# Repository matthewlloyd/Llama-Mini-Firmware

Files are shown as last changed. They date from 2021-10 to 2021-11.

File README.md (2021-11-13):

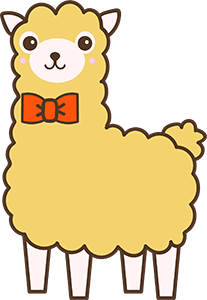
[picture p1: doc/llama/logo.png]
Llama Mini
# 

# Llama Mini

[]()

### Unofficial Firmware for the Prusa Mini and Mini+

One of Prusa's llamas escaped from HQ (:llama::running_man:) and decided to make his
own version of the firmware for the Prusa Mini. He's added quite
a few goodies:

* **Hotend fan speed**: Adds a menu option to unlock the hotend fan speed
  and increase it from the Prusa Firmware's default 38% to anywhere from 50-100%.
* **Skew compensation**: Turns on skew compensation in Marlin and allows it
  to be configured directly through the Settings menu or with `M852`.
* **OctoPrint screen**: Adds support for `M73` (print progress) and `M117`
  (LCD messages).
* **Sound**: Adds support for `M300` (play a sound).
* **PID tuning**: Automatically writes PID settings to EEPROM after `M303 U1` (autotune),
  `M301` (set hotend PID), and `M304` (set bed PID).
* **Max Temps**: Raises the maximum bed temperature from 100C to 110C
  and nozzle temperature from 290C to 300C (use with caution!).

All settings are automatically saved to EEPROM and loaded on boot.

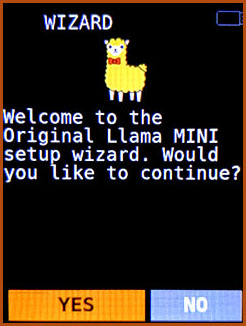
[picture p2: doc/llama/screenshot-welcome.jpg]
Welcome

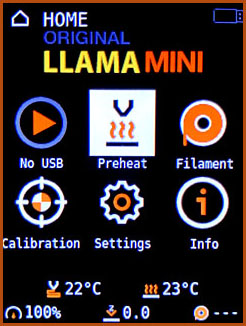
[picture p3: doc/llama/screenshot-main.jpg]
Main

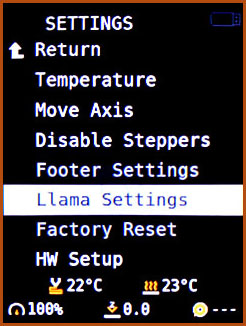
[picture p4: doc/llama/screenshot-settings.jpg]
Settings

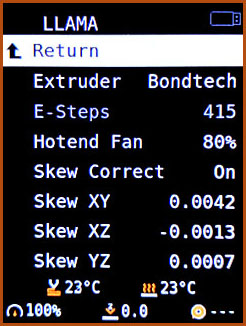
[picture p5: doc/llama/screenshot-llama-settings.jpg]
Llama Settings

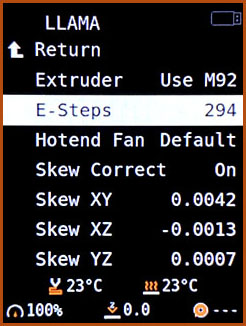
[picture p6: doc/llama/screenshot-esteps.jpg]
E-Steps

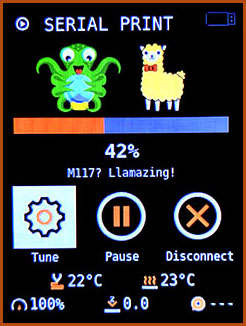
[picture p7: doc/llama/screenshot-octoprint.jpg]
Octoprint


#### Feed the Llama

This plugin is developed in my spare time. If you like it, please
consider supporting further development and updates by making a donation.



---

## Installing Livestock

### Jailbreak your Mini

You will need to cut out Prusa's appendix to install custom firmware.
Follow the instructions [here](https://help.prusa3d.com/en/article/flashing-custom-firmware-mini_14/).
This is irreversible and voids the warranty, although in the US
you are protected by the [Magnuson-Moss Warranty Act](https://www.ftc.gov/news-events/press-releases/2018/04/ftc-staff-warns-companies-it-illegal-condition-warranty-coverage).

Of course you could always buy a second Buddy board and let your Llama
run wild on that instead.

Alternatively, if you are good at very fine pitch soldering, you could
lift the BOOT0 pin off the board entirely and make your own jumpers
to connect it directly to 3.3V or GND as you need (the appendix merely
[shorts BOOT0 directly to GND](https://hackaday.com/2019/12/16/prusa-dares-you-to-break-their-latest-printer/)).

Once you have done that, you can live and let live-stock.

### Flash Llama

Whenever you install new firmware, it's good practice to make a note of your
settings first, particularly your Live Z Offset and your skew coefficients
if you already have Llama installed.

Download the latest release [here](https://github.com/matthewlloyd/Llama-Mini-Firmware/releases).
Copy the `.bbf` file to the root of your USB flash drive.
Follow the instructions [here](https://help.prusa3d.com/en/guide/how-to-update-firmware-mini-mini_128421/)
to install the firmware. The bootloader will warn you the signature is
incorrect - select "Ignore".

### First Run

If you lose your Prusa EEPROM settings during the upgrade process,
when you first run the firmware, Prusa will send you to the initial
calibration wizard. This can be a problem if you need to set custom e-steps
before printing anything. Just skip the initial setup wizard,
use the Llama Settings menu to configure your e-steps, and
then rerun the setup wizard manually.

### Livestock to Stock

Download Prusa's stock firmware [here](https://www.prusa3d.com/drivers/).
The bootloader might not let you downgrade the firmware unless you
explicitly give permission. Go to the Settings menu, scroll down to "FW Upgrade",
and change the option to "On Restart Older" (this option is only available
in Llama firmware).

To reflash the board in DFU mode, [see below](#flashing-in-dfu-mode).

---

## Configuration

To configure Llama settings, open the Settings menu and select "Llama Settings".
Llogical!

### Configuring E-steps

New in v1.0.7: This can now be done using Prusa's own "Experimental Settings" menu,
which is shown by default as a menu item next to "Llama Settings" in this firmware.

#### For Llama versions v1.0.6 and below

Select "Extruder" and click to select one of:

- **Prusa**. Stock e-steps for the stock extruder.
- **Bondtech**. Preset e-steps for the [Bondtech extruder upgrade](https://www.bondtech.se/product/prusa-mini/).
  This option assumes you have reversed the motor wiring as per Bondtech's instructions -
  if you haven't, you can reverse the extruder motor direction using the "Reverse E" option.
- **Custom**. The e-steps can be configured using the jog wheel, or by
  sending the `M92 E<steps>` command.

Whether you use a preset, or set custom e-steps via the jog wheel
or `M92`, your settings will automatically be saved to EEPROM.
You do not need to use `M500`.

### Configuring Hotend Fan Speed

The Prusa firmware limits the hotend fan speed to 38% because a happy user is a user with
an underperforming but quiet machine. The fan is capable of running at much
higher RPMs. There are a few reasons you might want to do this:

- Reduce heat creep.
- Print higher temperature filaments.
- Change the fan to one which requires full voltage, e.g. a Noctua.

This menu option allows you to set the hotend fan speed anywhere from 50% to 100%,
in 10% steps. The setting is automatically saved to EEPROM and restored on boot.

### Configuring Skew Compensation

The Prusa Mini+ is inherently prone to skew, by virtue of its cantilever
design. It is normal to see skew on all three axes. This affects the precision
of any parts you print.

Prusa disabled skew compensation in Marlin, because a happy user is a user
with an imprecise but easy to use machine. Lluckily our Llama has reenabled it.
All three skew compensation coefficients are available for use - I for XY, J for XZ,
and K for YZ.

Note it is always preferable to remove as much skew as possible through physical
adjustments before using firmware skew compensation. For excellent
instructions, read [this post on Prusa's forum](https://forum.prusaprinters.org/forum/hardware-firmware-and-software-help/oh-no-were-skewed-prusa-mini-edition/).

See [the section below](#calibrating-skew) for a guide on how to measure skew
and compute the coefficients. You can use the jog wheel to set
the coefficients in this menu, or use `M852`. Either way, the settings
will automatically be saved to EEPROM - you do not need to use `M500`.
Be sure to set `Skew Correct` to `On` for the settings to be used.

Be careful with large skew correction factors - it is possible to go past
the min or max travel on the X and Y axes while printing or even during
mesh bed leveling. A skew factor of e.g. 0.01 equates to
`0.01 * 180mm = 1.8mm` of movement at the far end of the bed,
so your usable print area will be reduced accordingly.

### Configuring PID Parameters

The stock firmware allows you to run an `M303` PID autotune, but the new
settings are lost on reset. In Llama, PID settings are *automatically* written
to EEPROM after any command that updates Marlin's PID values, which could be
an `M301` (set hotend PID), `M304` (set bed PID), or an `M303 U1` (autotune and
use the PID result). These values will then be restored on reset, too. You do not
need to use `M500`.

If you need to restore the default PID values, they can be reset by running
the following commands:

* Hotend: `M301 P7.00 I0.50 D45.00`
* Bed: `M304 P120.00 I1.50 D600.0`

Note that if you run `M303` (autotune) without the `U1` parameter, Marlin
will just print out the suggested PID values without changing the settings,
and they won't get written to EEPROM.

---

### Print Progress

Note that to take advantage of Llama's `M73` support with [OctoPrint](https://octoprint.org),
you will need to install one or more plugins. I recommend these three:

- [Print Time Genius](https://plugins.octoprint.org/plugins/PrintTimeGenius/),
  an excellent plugin to compute accurate progress estimates. It doesn't send
  `M73` or `M117` on its own, so you will need the next two plugins too.
- [DisplayLayerProgress](https://github.com/OllisGit/OctoPrint-DisplayLayerProgress).
  Turn on the "Printer Display" option and customize to your preference.
  This will send `M117`. I like to set the message to `[printtime_left] L=[current_layer]/[total_layers]`
  and the update interval to 10 seconds.
- [M73 Progress](https://plugins.octoprint.org/plugins/m73progress/).
  Be sure to enable the "Use time estimate" option.

It may also be possible to arrange for your slicer to insert these commands,
but the result will not be as accurate.

---

## Calibrating Skew

Measuring skew on all three axes at once can be done by simply printing
[this compact calibration tower](doc/llama/skew.stl):

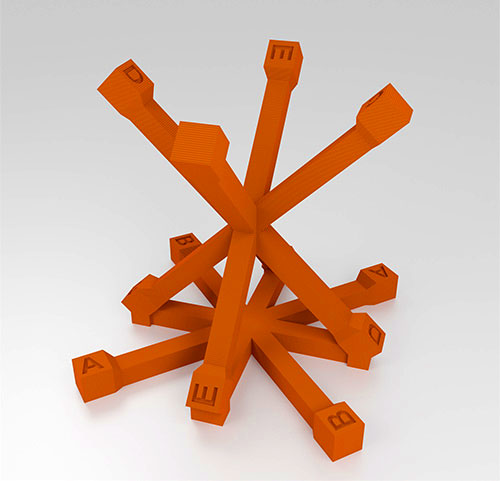
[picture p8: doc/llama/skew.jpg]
Skew Tower


Turn off skew correction before you print. Use a normal layer height
(0.15mm) and no supports. Do not rotate the model in your slicer -
it must be printed in the same orientation as supplied in the STL.

Then, make a copy of [this spreadsheet](https://bit.ly/2SJ1hAU).
Use [calipers](https://amzn.to/3vVRgOl) to measure the six diagonals,
conveniently labeled A to F, and type the measurements
into the spreadsheet. It will calculate your three skew correction factors.
You can either input them using the Llama menu and jogwheel as described above,
or send them directly to the printer using the supplied `M852` command.

If you want to check your calibration is accurate,
print the same tower with skew correction enabled. The diagonals should
then all have the same length (within measurement error of course).

---

### Flashing in DFU Mode

If the bootloader refuses to accept firmware from a USB flash drive,
it's possible to flash the board directly in DFU mode.

Compile the firmware and build a DFU file:

```
$ python3 utils/build.py --generate-dfu --bootloader yes
```

If you built it from another machine, copy it to your Pi:

```
$ scp build/mini_release_boot/firmware.dfu <user>@<pi-host>:~/
```

Put your Buddy board in DFU mode by placing a jumper across the relevant pins
and resetting. If you have a 3-pin header next to the appendix (older versions
of the board), put the jumper between BOOT0 and 3.3V. If you have a 2-pin header,
just add a jumper.

Then flash from your Pi:

```
$ lsusb
Bus 001 Device 010: ID 0483:df11 STMicroelectronics STM Device in DFU Mode
$ sudo apt install dfu-util
$ dfu-util -a 0 -D firmware.dfu
```

Don't forget to remove the jumper before resetting.

---

*Copyright (C) 2021 Matthew Lloyd*

## Original Prusa Mini Firmware README
<details>
<summary>Click to expand!</summary>

# Buddy

Build Status (https://holly.prusa3d.com/job/Prusa-Firmware-Buddy/job/Multibranch/job/master/)

This repository includes source code and firmware releases for the Original Prusa 3D printers based on the 32-bit ARM microcontrollers.

The currently supported model is:
- Original Prusa MINI

## Getting Started

### Requirements

- Python 3.6 or newer
- python3-pip

### Cloning this repository

Run `git clone https://github.com/prusa3d/Prusa-Firmware-Buddy.git`.

### Building (on all platforms, without an IDE)

Run `python utils/build.py`. The binaries are then going to be stored under `./build/products`.

- Without any arguments, it will build a release version of the firmware for all supported printers and bootloader settings.
- To generate `.bbf` versions of the firmware, use: `./utils/build.py --generate-bbf`.
- Use `--build-type` to select build configurations to be built (`debug`, `release`).
- Use `--printer` to select for which printers the firmware should be built.
- By default, it will build the firmware in "prerelease mode" set to `beta`. You can change the prerelease using `--prerelease alpha`, or use `--final` to build a final version of the firmware.
- Use `--host-tools` to include host tools in the build (`bin2cc`, `png2font`, ...)
- Find more options using the `--help` flag!

#### Examples:

Build the firmware for MINI in `debug` mode:

```bash
python utils/build.py --printer mini --build-type debug
```

Build _final_ version for all printers and create signed `.bbf` versions:

```bash
python utils/build.py --final --generate-bbf --signing-key <path-to-private-key>
```

Build the firmware for MINI using a custom version of gcc-arm-none-eabi (available in `$PATH`) and use `Make` instead of `Ninja` (not recommended):

```bash
python utils/build.py --printer mini --toolchain cmake/AnyGccArmNoneEabi.cmake --generator 'Unix Makefiles'
```
#### Windows 10 troubleshooting

If you have python installed and in your PATH but still getting cmake error `Python3 not found.` Try running python and python3 from cmd. If one of it opens Microsoft Store instead of either opening python interpreter or complaining `'python3' is not recognized as an internal or external command,
operable program or batch file.` Open `manage app execution aliases` and disable `App Installer` association with `python.exe` and `python3.exe`.

### Development

The build process of this project is driven by CMake and `build.py` is just a high-level wrapper around it. As most modern IDEs support some kind of CMake integration, it should be possible to use almost any editor for development. Below are some documents describing how to setup some popular text editors.

- [Visual Studio Code](doc/editor/vscode.md)
- [Vim](doc/editor/vim.md)
- [Eclipse, STM32CubeIDE](doc/editor/stm32cubeide.md)
- [Other LSP-based IDEs (Atom, Sublime Text, ...)](doc/editor/lsp-based-ides.md)

#### Formatting

All the source code in this repository is automatically formatted:

- C/C++ files using [clang-format](https://clang.llvm.org/docs/ClangFormat.html),
- Python files using [yapf](https://github.com/google/yapf),
- and CMake files using [cmake-format](https://github.com/cheshirekow/cmake_format).

If you want to contribute, make sure to install [pre-commit](https://pre-commit.com) and libtinfo5 and then run `pre-commit install` within the repository. This makes sure that all your future commits will be formatted appropriately. Our build server automatically rejects improperly formatted pull requests.

## Flashing Custom Firmware

To install custom firmware, you have to break the appendix on the board. Learn how to in the following article https://help.prusa3d.com/article/zoiw36imrs-flashing-custom-firmware.

## Feedback

- [Feature Requests from Community](https://github.com/prusa3d/Prusa-Firmware-Buddy/labels/feature%20request)

## License

The firmware source code is licensed under the GNU General Public License v3.0 and the graphics and design are licensed under Attribution-NonCommercial-ShareAlike 4.0 International (CC BY-NC-SA 4.0). Fonts are licensed under different license (see [LICENSE](LICENSE.md)).
</details>

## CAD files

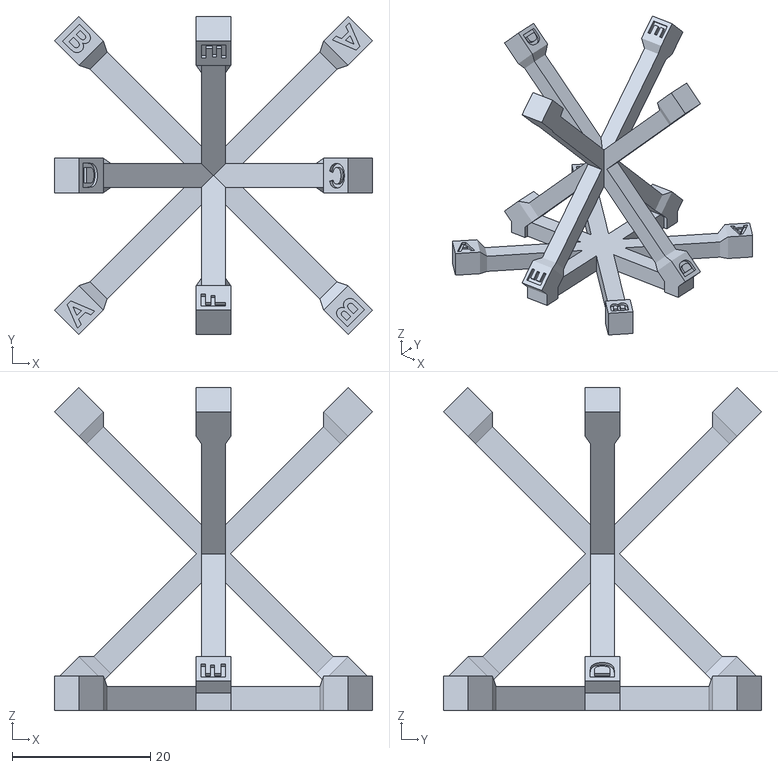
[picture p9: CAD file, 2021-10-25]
doc/llama/skew.stl
46.0 x 46.0 x 46.7

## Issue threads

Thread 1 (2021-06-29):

FR: Stealthchop mode for Extruder for Quieter Operation

talldonkey, 2021-06-29:
FR is for overall end goal for a quieter printer

Hypothesis:  Switching Extruder to Stealthchop will make it quieter, and hopefully doesn't have downsides.

The stock prusa mini firmware has the Extruder in spreadcycle mode.  I believe the X Y Z axis are already in stealthchop.
There may be an theoretical opportunity to quiet the extruder down by switching the extruder to stealthchop.  This may require tweaks such as upping the extruder current a bit for reliable operation, if it doesn't work at stock current.

matthewlloyd, 2021-07-07:
I won't have a chance to implement this personally but I'm happy to review any related pull requests. It would need to be made optional and adjustable via the settings menu, and tested to make sure the extruder doesn't skip even more steps than it already does.

espr14, 2022-12-20:
`M569 S1 E` command should do the work.

matthewlloyd, 2023-02-04:
Thanks for opening an issue. Unfortunately since I am no longer have time to maintain this project, I am closing all PRs and issues so that I can archive the repository.

Closed 2023-02-04.

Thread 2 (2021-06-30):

Adjust Z Height Test in Wizard

dcs3473, 2021-06-30:
For those using the Mini Silicone Bed Level fix the default Z height may be to high.  This gives you a fail during the wizard setup process.  It proceeds and will continue to work fine but just seeing the error causes anxiety.  Im not sure exactly how you could adjust for this as some users may have different heights based on how they cut the silicone pieces.

matthewlloyd, 2021-07-07:
This should be fixed by adjusting the height of the PINDA sensor as part of any hardware modifications made to the bed. Not much to do here on the firmware side.

Closed 2021-07-07.

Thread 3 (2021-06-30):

M303 E-1 Bed Pid Fails

dcs3473, 2021-06-30:
When trying to do an M303 E-1 S? (any temp) fails with a message of...

Send: M303 E-1 S50 U1
Recv: PID Autotune failed! Temperature too high

Doesn't matter what temp you try, 50, 60, 70 they all fail.

matthewlloyd, 2021-07-04:
This is caused by a bug in Prusa's version of Marlin: https://github.com/prusa3d/Prusa-Firmware-Buddy/issues/798

The workaround is to use E-2 instead of E-1, e.g. `M303 E-2 S50 U1`.

Closed 2021-07-04.

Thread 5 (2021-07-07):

[BUG] Bootloop

felixhesshaw, 2021-07-07:
Hello,

I can't get the custom firmware to work with my prusa mini:
After building the firmware, I flashed the bbf file in bootloader mode. This worked normally but then I ended up in a bootloop shortly after that.

Tried your bbf file too, but didn't succeed to boot the prusa normally...

Have anyone else this problem?

Best regards and thanks for your work
Felix

matthewlloyd, 2021-07-07:
I haven't had that issue. What command did you use to build the BBF? At what point does it reset during the bootloop (perhaps upload a video on YT or something)? Are you running an Original Mini or a clone, and what version is the bootloader?

You can always build and flash in DFU mode, which will update the bootloader to the latest version (v1.1). There are instructions here: https://github.com/matthewlloyd/Llama-Mini-Firmware#flashing-in-dfu-mode

felixhesshaw, 2021-07-09:
Hey Matthew,

thanks for your quick reply!
I used this command that I know from the original firmware:
python utils/build.py --final --generate-bbf

Here is a video from the flashing process and the bootloop:
https://streamable.com/ysm7o6

My Prusa Mini is a chinese Clone but I have successfully flashed the original firmware with a few modifications in Configuration_A3ides_2209_MINI.h (like bondtech extruder, PID and thermistor settings).

My bootloader is 1.0.0. I will try to flash in DFU Mode.
Is it possible to revert to original firmware then?

Thanks for your help!

matthewlloyd, 2021-07-09:
I would guess one of these is the issue:

- Bootloader offset. The command you use builds three variants, mini_release_noboot, mini_release_emptyboot, and mini_release_boot. You didn't specify which one you flashed, but only one of these will work (mini_release_emptyboot I think). This is because the code uses absolute addressing, and the start address of the firmware changes depending on the variant. The bootloader always flashes the BBF at a fixed address, so if the code is compiled assuming it starts at a different address, it won't work. This is the most likely explanation.
- Something related to EEPROM size. The Chinese clone may use a smaller EEPROM than the original, so the EEPROM settings might not work correctly. This is unlikely.

It's always possible to revert to the original firmware. Flashing in DFU is the same as flashing with the bootloader, just doing it at a lower level and bypassing the bootloader entirely. The file format is also different (standard DFU, vs Prusa's proprietary BBF). It's the only way to upgrade the bootloader as far as I know (Prusa hasn't released the source code for the bootloader, so who knows).

felixhesshaw, 2021-07-09:
Hey,

I flashed the bbf from emptyboot and tried your release bbf too. I hope it's not the EEPROM ;) That would be really annoying.

Next thing I want to try is building the firmware in debug mode and hope to get some infos about the error.

Do you think it is the outdated bootloader that causes this problem?

matthewlloyd, 2021-07-09:
You could also try cloning the original Prusa firmware repo and building the BBF from that using the exact same command. If that doesn't work either, then it probably anything related to Llama, i.e. it isn't the extra EEPROM space. If this doesn't work, but it does work if you flash with the official BBF, then there's something up with the way you're building it.

Unfortunately without connecting an ST-Link to the SWD debug pins it will be hard to figure out. The error occurs too early to get anything useful out of the USB or serial ports.

Outdated bootloader could cause the issue but seems unlikely. I would probably upgrade by DFU anyway to be sure.

qp0n4ik, 2021-07-10:
Hey do you have any luck flashing it? I have the same problem, but I have no idea how to flash it in DFU, could you please help me?

felixhesshaw, 2021-07-10:
Didn't tried it with dfu. I decided to stay with my own modified firmware based on the original from prusa. Had no trouble flashing the bbf with that.
Lost a little bit hope with this custom rom despite the features sound really appealing with skew correction and hot end rpm control.

qp0n4ik, 2021-07-10:
> Didn't tried it with dfu. I decided to stay with my own modified firmware based on the original from prusa. Had no trouble flashing the bbf with that.
> Lost a little bit hope with this custom rom despite the features sound really appealing with skew correction and hot end rpm control.

How did you fix the bootloop?

qp0n4ik, 2021-07-10:
Could help me please? Im in constant bootloop and I cant do anything, i could tip you in paypall for your time

felixhesshaw, 2021-07-10:
I just flashed the "old" bbf from my modified prusa firmware.
You can use the original bbf file as well:

Just put it on an usb drive and insert it into your prusa mini.
Then turn on the printer and immediatly push the wheel button several times.
Then you confirm the flashing and you are done.

Feel free to ask again if you're still stuck.

felixhesshaw, 2021-07-10:
Here is a guide line for flashing the firmware (Step 8):
https://help.prusa3d.com/en/guide/how-to-update-firmware-mini-mini_128421

qp0n4ik, 2021-07-10:
oh wow!!!!!  I didn't know about  that "immediately push the wheel button several times"
thank you for saving me money I thought I have to buy new board now.

May I ask you to try your custom firmware?  the only reason I wanted this on is to change e-steps because I just installed new bondtech extruder

matthewlloyd, 2021-07-11:
I just released v1.0.4 which fixes a small bug I just noticed, which could in theory cause a bootloop on some devices. I don't know whether this actually is the cause of your bootloop, but if you like you can give it a try once you're comfortable switching between firmwares.

felixhesshaw, 2021-07-11:
Hey Matthew,
I flashed the new version successfully! Big thanks to you for this fix.

@qp0n4ik Do you want to give the fixed version a try? I can compile a modified version of the original prusa for you. But I don't think this thread is the right place for this. Maybe try the fixed version first ;)

matthewlloyd, 2021-07-11:
> I flashed the new version successfully! Big thanks to you for this fix.

Very glad to hear it, and good to know this was the issue after all - sorry for the bug and thanks for your patience.

Closed 2021-07-10.

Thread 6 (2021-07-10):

[BUG]<Bootloop plz help>

qp0n4ik, 2021-07-10:
I have flashed the file from USB flashcard, and now I have constant bootloop, i have no idea how to reflash it in the DFU mode? could anyone make video of the process? do I need raspberry pi for that? I have original prusa mini
I have very limited knowledge and don't understand "Flashing in DFU Mode"  instruction with python code, i could tip if anyone can help me, I really don't want to spent 100$ for new board.
P.S. I did break appendix before everything else and put black jumper on  BOOT0 and GND

matthewlloyd, 2021-07-10:
Did you put the jumper back to its original position? That seems like the most likely explanation.

Unfortunately I have limited time to offer to support the hardware of Prusa Buddy boards and bootloader issues - I recommend contacting Prusa support directly for assistance with the appendix, jumpers, and flashing.

qp0n4ik, 2021-07-10:
Why you closed the topic? No, I did not put a jumper on original place.

matthewlloyd, 2021-07-11:
I just released v1.0.4 which fixes a small bug I just noticed, which could in theory cause a bootloop on some devices. I don't know whether this actually is the cause of your bootloop, but if you like you can give it a try once you're comfortable switching between firmwares.

Closed 2021-07-10.

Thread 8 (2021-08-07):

[BUG] "Print fan not running" error

Greeneyedblackcat, 2021-08-07:
Please, before you create a new bug report, please make sure you searched in open and closed issues and couldn't find anything that matches.

**Printer type** - [MINI]

**Printer firmware version**-  v1.0.5 (based on Prusa buddy 4.3.2-RC1)

**Original or Custom firmware** [Original/Custom]

**Optional upgrades** - Runout sensor

**USB drive or USB/Octoprint**
  Please let us know if you print via USB flash drive or USB/Octoprint

**Describe the bug**
I am having a print fan not running  error come up within the first 4% of the print about five times, my print fan is running, after I clear it five times it will run the rest of the print without a single error. When I switch back to factory prusa firmware the problem goes away. My mini is brand new, I checked the plug, connections and I Ohmed out the wires with a multi meter and they are verified good. I love your Llama Firmware and wish to continue to use it.   Any assistance you could provide me on this matter would be greatly appreciated.       Regards JJK

**How to reproduce, Simply start a print . Like clockwork Print fan errors,
**Expected behavior**
  A clear and concise description of what you expected to happen.

**G-code**
  Please attach the G-code you had trouble with. This will make it easier for us to replicate the error.

**Crash dump file**
  Please attach the crash dump file. This will make it easier for us to investigate the bug.

**Video**
  Please attach a video. It usually helps to solve the problem.

matthewlloyd, 2021-08-07:
I'm pretty sure this is a bug in 4.3.2-RC1 on Prusa's side because I haven't made any changes that would affect the print fan code. What specific version of factory Prusa firmware are you switching back to? You can check in the Settings menu or in the bootloader screen.

Greeneyedblackcat, 2021-08-07:
Matthew, Thank you so much for the Quick reply. I'm pretty sure its on Prusas end.  The Prusa firmware is 4.3.1,  I really want to keep your Llama firmware, do you think I could simply download one of your previous versions of Llama to fix this problem,  I may try one of your previous versions, you have done a spectacular job with this Firmware. Don't get me wrong I'm not bitching I am grateful to have it bugs and all.  Thanks again for the Reply.

matthewlloyd, 2021-08-07:
All the Llama versions so far are based on 4.3.2-RC1, so they will all have this issue. The best hope would be to reproduce the bug with Prusa's own 4.3.2-RC1, open an issue on their GitHub, and wait for them to fix it as they prepare to release 4.3.2 final. Once Prusa releases 4.3.2 final, I'll release a new version of Llama.

Greeneyedblackcat, 2021-08-07:
Sounds great, I can just deal with the bug until 4,3,2 final. Thank you so much for your time and effort on these Mini's.  I am a  barely computer literate Safecracker by trade and I Thank god there are computer Geniuses like yourself on this planet, Looking forward to 4.3.2 final in Llama.

matthewlloyd, 2021-08-14:
I released v1.0.6, based on 4.3.2-final from Prusa. Let me know if it fixes this issue for you.

Greeneyedblackcat, 2021-08-14:
Thank you so much. I will install it and let you know. Thanks again for
your help.    Regards.  James Keenan

On Sat, Aug 14, 2021, 2:40 PM Matthew Lloyd ***@***.***>
wrote:

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

matthewlloyd, 2021-09-16:
This is over a month old, I'm going to close. If it's not fixed, please let me know.

Greeneyedblackcat, 2021-09-16:
Matthew its fixed. Thank you so much.  Regards.  JK

On Thu, Sep 16, 2021, 1:41 PM Matthew Lloyd ***@***.***>
wrote:

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

Closed 2021-09-16.

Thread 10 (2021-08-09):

Ability to name sheets

audiorazor, 2021-08-09:
First off, thank you for making this firmware.   Feels good to have control over my printer again.

Do you think there is any way you could modify it so we can actually name the steel sheets?

espr14, 2022-12-20:
This should come with original FW. Probably with Prusa XL release.

matthewlloyd, 2023-02-04:
Thanks for opening an issue. Unfortunately since I am no longer have time to maintain this project, I am closing all PRs and issues so that I can archive the repository.

Closed 2023-02-04.

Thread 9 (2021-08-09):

[BUG]<First layer calibration >

Sorav1, 2021-08-09:
Hi this is Sorav here and I installed the firmware for testing. On doing calibration I went ahead with the repeat of first layer calibration ,on doing that the bed starts cooling down and it never starts heating .I need to reset from the LCD to do that again.

Sorav1, 2021-08-16:
In the latest firmware the issue got resolved.

matthewlloyd, 2021-08-16:
Glad to hear it, thanks for closing!

Closed 2021-08-16.

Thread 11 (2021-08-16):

[BUG]<Mesh bed leveling  hangs the system>

Sorav1, 2021-08-16:
Sir, I have installed the latest version of your firmware but when I do mesh calibration from lcd the system hangs and I need to reset all the time. The issue is not there with original Prusa firmware.

Sorav1, 2021-08-16:
https://youtu.be/JloiyZ9ovZA

matthewlloyd, 2021-08-17:
Do you have skew coefficients enabled? That could potentially cause an out-of-bounds move. Just a hypothesis.

Please connect OctoPrint or some other G-Code terminal and see if there is any error output.

Sorav1, 2021-08-20:
Hi greetings of the day.
I have tried keeping skew coefficients disabled/enabled but still the same issue.

Sorav1, 2021-08-20:
Will connect the machine to pronteface and update you the results.

matthewlloyd, 2021-09-16:
This is a month old, I'm going to close. If it's not fixed, please let me know.

Closed 2021-09-16.

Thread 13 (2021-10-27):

[QUESTION] Enabling SWD firmware debugging on Prusa mini/buddy board

matterenergy, 2021-10-27:
Hi Matthew,
Could you provide some details re: how you were able to do SWD debugging of the firmware on the buddy board (Prusa Mini) while developing the Llama-Mini-Firmware?

I'm able to debug a STM32F4-Discovery with an identical STM32F407VG MCU, but not the actual printer's buddy board.
The board has the "appendix" removed.
Using the SWD debug connector of the buddy board.
nRST resets the board but does not halt it, not really allowing debugging or SWD firmware flashing.

Prusa's site/forum do not appear helpful in this regard (SWD debugging).
Perhaps you can share some of your findings.

Thank you

matthewlloyd, 2023-02-04:
Thanks for opening an issue. Unfortunately since I am no longer have time to maintain this project, I am closing all PRs and issues so that I can archive the repository.

Closed 2023-02-04.

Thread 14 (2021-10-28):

Custom extruder esteps greater than 500

buenso, 2021-10-28:
Hello @matthewlloyd

After replacing the stock extruder with a pancake nema 17 (direct drive) , my esteps need to be set to 830

It seems that the max setting in the lcd menu is 500, and if I try to write to eeprom with M92 E830 and M500, it seems that nothing is saved?

I did create a gcode with these parameters, and saved to usb and then hit print, but every time i reboot the printer, it changes back to default value?

Is it possible to unlock the max value of 500 in the lcd menu?

espr14, 2022-12-20:
Try the latest version but look into `Settings -> Experimental Settings`. You can set 1 to 1000.

matthewlloyd, 2023-02-04:
Thanks for opening an issue. Unfortunately since I am no longer have time to maintain this project, I am closing all PRs and issues so that I can archive the repository.

Closed 2023-02-04.

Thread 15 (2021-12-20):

[FEATURE REQUEST] Higher density mesh bed leveling

bbbenji, 2021-12-20:
Please add the option to configure the number of MBL measurement points.

I see it has been requested and implemented in the MK3 firmware here: https://github.com/prusa3d/Prusa-Firmware/issues/1239
as well as requested for the Mini in the original FW repo here: https://github.com/prusa3d/Prusa-Firmware-Buddy/issues/1492

In addition to the above, it would be cool to set a 3x3 mesh that measures at the exact location of each heatbed mounting point.

If such a feature was to be implemented, I would gladly update the G29 absolute values to relative converter: https://bbbenji.github.io/PMSBLM/

espr14, 2022-12-21:
The main issue is the location of magnets which interfere with the PINDA. If you want different count of points you have to find proper places. Otherwise, the measurement will be worse.

Eldenroot, 2022-12-22:
@espr14 I would like to see at least 20 or 24 mesh leveling

espr14, 2022-12-23:
25 (5x5) points would make sense for squared bed.

matthewlloyd, 2023-02-04:
Thanks for opening an issue. Unfortunately since I am no longer have time to maintain this project, I am closing all PRs and issues so that I can archive the repository.

Closed 2023-02-04.

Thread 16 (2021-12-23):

[FEATURE REQUEST]<Enter comprehensive title>

SirDobrotivy, 2021-12-23:
Please create an option to resize the bed. I would like to enlarge the printable area.
Also, please specify that the bed is not heated. Unfortunately, the calibration is set to require heating.

matthewlloyd, 2023-02-04:
Thanks for opening an issue. Unfortunately since I am no longer have time to maintain this project, I am closing all PRs and issues so that I can archive the repository.

Closed 2023-02-04.

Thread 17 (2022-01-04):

[ENHANCEMENT] PID autotune

Fra085, 2022-01-04:
Printer type: MINI
Optional upgrades: PID autotune

It would be great if there was an easy way to manage PID autotune from the main menu.
At the moment it is only possible to perform it through gcode, or am I wrong?

Thanks a lot for your work, bringing us wonderful features.

matthewlloyd, 2023-02-04:
Thanks for opening an issue. Unfortunately since I am no longer have time to maintain this project, I am closing all PRs and issues so that I can archive the repository.

Closed 2023-02-04.

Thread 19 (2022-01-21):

[FEATURE REQUEST] Update with Buddy Firmware 4.3.4

dimitribellini, 2022-01-21:
Do you think we can have your modded firmware based on Prusa Buddy 4.3.4?
Thanks

Eldenroot, 2022-10-26:
Any news???

espr14, 2022-12-21:
Ready to pull #30.

espr14, 2022-12-31:
Here's 4.3.4 with extras:
- fixed skew
- Llama settings available during printing
- Nozzle cooling by fan (`M109 R170 C`)
- game Snake

[Llama_MINI_4.3.4_extra.zip](https://github.com/matthewlloyd/Llama-Mini-Firmware/files/10327981/Llama_MINI_4.3.4_extra.zip)

prongato, 2023-01-01:
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

Thank you for this!  It’s awesome to have an updated version of Llama!

espr14, 2023-01-04:
@matthewlloyd Will you release this version or do you agree with moving this project to a shared repository? I don't want to just fork the development. This would be confusing for the users (where is the latest version, where to put issues etc.). What do you think?

matthewlloyd, 2023-01-04:
> @matthewlloyd Will you release this version or do you agree with moving this project to a shared repository? I don't want to just fork the development. This would be confusing for the users (where is the latest version, where to put issues etc.). What do you think?

Thanks for your efforts. Given time constraints on my side I think the only course of action open at this time is for you to start a fork. I am happy to add a link to your fork to the README of this repo.

Please note that since this repo is under GPLv3 and you have shared a derived binary above `Llama_MINI_4.3.4_extra.zip`, you need to provide the source code used to build it. I know you have opened PRs for some of these features, but you need to provide a link to a branch or a source archive that contains the complete source code for your binary distribution, including all extras you have added (including the Snake game).

espr14, 2023-01-06:
Now it's forked and released:

https://github.com/Llama-FW/Llama-P32-FW/releases/tag/v4.3.4a

matthewlloyd, 2023-02-04:
Thanks for opening an issue. Unfortunately since I am no longer have time to maintain this project, I am closing all PRs and issues so that I can archive the repository.

Closed 2023-02-04.

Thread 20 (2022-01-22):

Skew compensation doesn't work

dagov42, 2022-01-22:
**Printer type** - MINI+ with SuperPinda

**Printer firmware version**-  v1.0.7 (based on Prusa Buddy 4.3.3-final)

**Custom firmware - Llama

**Optional upgrades** - Filament Runout Sensor

**USB drive or USB/Octoprint**
  USB and Octoprint

**Describe the bug**
  I printed more than 20 test to compensate XY skew. And increase XY coefficient from 0.02 to 0.1. And diagonals length didn't change. I think this function isn't working.
A -  142.04
B - 140.65
I restore settings to default after install Llama firmware after original.
Tried to print via OctoPrint and USB.

SiegelDaniel, 2022-03-02:
Did you store settings to EEPROM ?

dagov42, 2022-03-02:
Yes, skew compensation works only in bed leveling mode, after that printer start printing - it doesnt work.

SiegelDaniel, 2022-03-04:
I've noticed the same problem with mine. I did the skew test print, logged in the values the spreadsheet gave me and afterwards the results remained the same. @matthewlloyd  Is this known yet?

matthewlloyd, 2022-03-04:
It's not known. I don't have a Prusa Mini any more so it's impossible for me to test and debug personally. I haven't made any changes to the skew correction code but it's possible Prusa changed something in the latest firmware which broke it when I rebased the changes. Certainly it was working on the previous version. I did take a quick look through the source code and see no reason why it would be broken. So this will need to be figured out by someone else.

Some debugging ideas:

- Have you tried setting a high correction value with e.g. "M852 I0.20" then verifying that a square comes out as a parallelogram, either in a real print or manually with LCD-menu moves or "G1 X... Y..." commands?
- Are your skew settings showing up in M503?
- Do you have anything in your slicer's start G-code which could reset the settings?

SiegelDaniel, 2022-03-04:
Thank you for replying that quickly.

Regarding the slicer's start G-CODE:
`M862.3 P "[printer_model]" ; printer model check
G90 ; use absolute coordinates
M92 E415
M83 ; extruder relative mode
M104 S170 ; set extruder temp for bed leveling
M140 S[first_layer_bed_temperature] ; set bed temp
M109 R170 ; wait for bed leveling temp
M190 S[first_layer_bed_temperature] ; wait for bed temp
M204 T1250 ; set travel acceleration
G28 ; home all without mesh bed level
G29 ; mesh bed leveling
M204 T[machine_max_acceleration_travel] ; restore travel acceleration
M104 S[first_layer_temperature] ; set extruder temp
G92 E0
G1 Y-2 X179 F2400
G1 Z3 F720
M109 S[first_layer_temperature] ; wait for extruder temp

; intro line
G1 X170 F1000
G1 Z0.2 F720
G1 X110 E8 F900
G1 X40 E10 F700
G92 E0

M221 S95 ; set flow`

Using pr0nterface, the skew settings do show up in M503. However, there is no reply from the printer on the M500 command.
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

I will try the high correction value now and report back in an hour.

dagov42, 2022-03-04:
Have you tried setting a high correction value with e.g. "M852 I0.20" then verifying that a square comes out as a parallelogram, either in a real print or manually with LCD-menu moves or "G1 X... Y..." commands?
 - Yes, I set 0.9 koefficient and probing failed cause probing mesh has distorsion and head goes away. I used lesser koeffcients around 0.2, mesh deformates but square diagonals doesn't change.
Are your skew settings showing up in M503?
- Yes, its the same settings as I set from display.
Do you have anything in your slicer's start G-code which could reset the settings?
 - No, I use start codes but it's not correct this settings.

SiegelDaniel, 2022-03-04:
I've verified with I=0.2 that the probe does indeed run off of the bed, which is why probing fails. I'm now trying with 0.1 again.
So it's safe to say that during probing / bed leveling the skew correction is certainly taking place.

matthewlloyd, 2022-03-04:
Ok, so the skew correction is clearly working in general, but might not be working when actually printing. Printing with a high correction factor to make the effect obvious, but not so high as to break mesh leveling, may be a good idea. Maybe the skew correction is being reset or turned off somehow by the Prusa firmware at the start of a print. Some more debugging ideas:

- Try printing (a) from SD card, and compare to (b) printing via OctoPrint. Skew correction might be working in one but not the other.
- Put an M503 in the G-Code you are printing, and check the output - i.e. after the print has already started.
- Put the M852 I command in the G-Code to see if that makes a difference.

SiegelDaniel, 2022-03-04:
Hi, I've printed the skew correction print with 0.1 for XY skew and it did not change a thing.
I'll try the other two hints tommorrow, that are great ideas. Thank you very much.

SiegelDaniel, 2022-03-24:
Hi, I've recently tried setting the skew correction again AFTER bed leveling in the printer's start GCODE.
However, there seems to be some calculation error as a minor correction of 0,0015 on XY results in the print being placed at a whole different position on the bed.

Do you have any ideas why that might be?

espr14, 2022-12-21:
Fixed in #29.

espr14, 2022-12-21:
> Hi, I've recently tried setting the skew correction again AFTER bed leveling in the printer's start GCODE. However, there seems to be some calculation error as a minor correction of 0,0015 on XY results in the print being placed at a whole different position on the bed.
>
> Do you have any ideas why that might be?

Skew center is in [0,0,0] not in the bed center. So if you print with Y = 100, there will be some X shift.

espr14, 2022-12-31:
Try this version https://github.com/matthewlloyd/Llama-Mini-Firmware/issues/19#issuecomment-1368281897.

espr14, 2023-01-11:
Or go directly to new project where the development will continue:
https://github.com/Llama-FW/Llama-P32-FW/releases/tag/v4.4.01

matthewlloyd, 2023-02-04:
Thanks for opening an issue. Unfortunately since I am no longer have time to maintain this project, I am closing all PRs and issues so that I can archive the repository.

Closed 2023-02-04.

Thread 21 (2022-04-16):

[FEATURE REQUEST] Power Outage Recovery

Fra085, 2022-04-16:
Is it possible to implement the power loss recovery feature like the MK3 for example? Prusa promised this long ago but never happed for the MINI. It would be great to see this implemented in your firmware.

Thanks a lot.

SiegelDaniel, 2022-04-16:
@Fra085 To my understanding @matthewlloyd does not continue development for this firmware as he does not own a Prusa Mini anymore.

 I will try and port the llama firmware to the newest Marlin Version in June / July 2022 and will make the necessary changes for power loss too.

Fra085, 2022-04-16:
Oh ok, thank you. I will wait for your release then.

espr14, 2022-12-21:
Power loss is tricky for MINI because it lacks the HW device which is in MK3. There has to be different approach (voltage/current drop). This could appear in the original FW in the future.

matthewlloyd, 2023-02-04:
Thanks for opening an issue. Unfortunately since I am no longer have time to maintain this project, I am closing all PRs and issues so that I can archive the repository.

Closed 2023-02-04.

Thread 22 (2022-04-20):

[QUESTION] Why does it have to be all llama related

crispyJim, 2022-04-20:
Please, before you create a new question, please make sure you searched in open and closed issues and couldn't find anything that matches.

**Leave your comments or questions here.**
can you please make it a normal firmware update instead of turning my entire prusa mini into a llama machine? I am angry that the only way to be able to play m300 sounds is turning my entire 3d printer into some stupid llama thing.

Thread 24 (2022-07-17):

Setting motor currents

SiegelDaniel, 2022-07-17:
Hello,

As I currently did a upgrade to the bear frame, the hardcoded motor current does not suffice anymore for Z.

Where exactly can I edit the motor currents? M907 does not work.

thanks in advance!

espr14, 2022-12-21:
Try `M906`.

matthewlloyd, 2023-02-04:
Thanks for opening an issue. Unfortunately since I am no longer have time to maintain this project, I am closing all PRs and issues so that I can archive the repository.

Closed 2023-02-04.

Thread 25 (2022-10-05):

[FEATURE REQUEST] Change Load/Unload feed length

dagognatt, 2022-10-05:
Having changed the bowden tube when upgrading extruder, I ended up with a bit shorter bowden tube than the original. This leads to the loading-procedure ramming filament into the hotend at full speed before starting the purge process.

It would be nice to see an option to adjust the length of the fast-feeding part of loading filament. (If this firmware is still active)

espr14, 2022-12-21:
Makes sense for direct drive mods as well.

Eldenroot, 2022-12-22:
Good idea

topchiyev, 2022-12-25:
Definitely a good idea!

matthewlloyd, 2023-02-04:
Thanks for opening an issue. Unfortunately since I am no longer have time to maintain this project, I am closing all PRs and issues so that I can archive the repository.

Closed 2023-02-04.

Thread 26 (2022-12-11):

[ENHANCEMENT]update based on 4.4.0 fw

g8toparadise, 2022-12-11:
**Printer type** - [MINI]
Since 4.4.0 FW is out will you update your llama?
Unless you wait for a more stable release.

threepoint2, 2022-12-14:
i understand matthew lloyd sold his prusa mini and stopped developing this firmware; unless someone forks it and updates it, this is now dead.

espr14, 2022-12-21:
There are tons of changes. This will take some time.

Eldenroot, 2022-12-21:
Maybe better to create a PR for Official firmware and implement.some.features to base.

espr14, 2022-12-22:
4.4.0 is the biggest change for MINI (bigger BBF, WiFi etc.) since the beginning so it will need some proper testing.
PR #31

espr14, 2022-12-23:
Happy Christmas, here's gift for you.
@matthewlloyd PR #31 is ready for review. It compiles but I haven't tested it yet.
Any volunteer to test OctoPrint screen and connection?
4.4.0 removes 102,000 lines while adds 770,000 lines of code.

Eldenroot, 2022-12-23:
Great, thx

espr14, 2022-12-24:
Here's the [FW_MINI_Llama_alpha_based_on_4.4.0.zip](https://github.com/matthewlloyd/Llama-Mini-Firmware/files/10298302/FW_MINI_Llama_alpha_based_on_4.4.0.zip)

Eldenroot, 2022-12-24:
Thank you. What about other PRs  - are included or not?

espr14, 2022-12-24:
Other PRs are not in this.

prongato, 2022-12-25:
> Here's the [FW_MINI_Llama_alpha_based_on_4.4.0.zip](https://github.com/matthewlloyd/Llama-Mini-Firmware/files/10298302/FW_MINI_Llama_alpha_based_on_4.4.0.zip)
> Press knob during start to force loading. Bootloader >2.0.0 is needed. If you don't have it, install original FW 4.4.0 first.

I will help test it!  I have been so excited for this firmware because I am running a Mosquito and use the PID auto tune and like writing it to the EEPROM.  I will install it tomorrow.  What for format, etc do you want error reporting in?

prongato, 2022-12-25:
> Here's the [FW_MINI_Llama_alpha_based_on_4.4.0.zip](https://github.com/matthewlloyd/Llama-Mini-Firmware/files/10298302/FW_MINI_Llama_alpha_based_on_4.4.0.zip)
> Press knob during start to force loading. Bootloader >2.0.0 is needed. If you don't have it, install original FW 4.4.0 first.

BTW, if you plan on possibly taking over or forking Llama, just tell me where to donate!  I fell in love with this version of firmware because I like to tinker with my Mini and the default firmware is locked down.

do you know if they’ve fixed the mesh level bug on 4.4.0 yet?

prongato, 2022-12-28:
> Here's the [FW_MINI_Llama_alpha_based_on_4.4.0.zip](https://github.com/matthewlloyd/Llama-Mini-Firmware/files/10298302/FW_MINI_Llama_alpha_based_on_4.4.0.zip)
> Press knob during start to force loading. Bootloader >2.0.0 is needed. If you don't have it, install original FW 4.4.0 first.

- Tried to update the firmware on my Mini and get this error when rebooting [https://imgur.com/a/DkEHS01](url)

espr14, 2022-12-30:
There's a plan to create indepentent repository. I'll let you know then. I think the bug is not fixed and won't be fixed soon because of XL release.

I'll look at the error. But it seems it won't be easy so it won't be soon.

prongato, 2022-12-31:
> There's a plan to create indepentent repository. I'll let you know then. I think the bug is not fixed and won't be fixed soon because of XL release.
>
> I'll look at the error. But it seems it won't be easy so it won't be soon.

Good to know.  I’m available and willing to help with any testing.  No hurry for me, I would prefer you port a latter release anyway because 4.4.0 has a mesh level bug I don’t think they’ve addressed yet.

My biggest concern is a semi-consistent place to obtain unlocked firmware for my Mini so I have access to PID auto tunes, skew corrections, the ability to control the hotend fan percentage (I run a Slice Mosquito with a 25mm 5v fan on mine).   I appreciate any work you put into maintaining this firmware.  If you need donations or any support I can offer, please just let me know.

espr14, 2022-12-31:
Meanwhile, there's version based on 4.3.4 https://github.com/matthewlloyd/Llama-Mini-Firmware/issues/19#issuecomment-1368281897.

espr14, 2023-01-11:
Here's Llama's v4.4.01
https://github.com/Llama-FW/Llama-P32-FW/releases/tag/v4.4.01

espr14, 2023-01-19:
Here are the latest releases.
@prongato You can donate here: https://www.patreon.com/espr14

matthewlloyd, 2023-02-04:
Thanks for opening an issue. Unfortunately since I am no longer have time to maintain this project, I am closing all PRs and issues so that I can archive the repository.

Closed 2023-02-04.

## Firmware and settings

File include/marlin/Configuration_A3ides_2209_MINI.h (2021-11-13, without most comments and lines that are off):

#pragma once
#define CONFIGURATION_H_VERSION 020000
#define USE_PRUSA_EEPROM_AS_SOURCE_OF_DEFAULT_VALUES
    #include "eeprom_function_api.h"
#define STRING_CONFIG_H_AUTHOR "(none, default config)" // Who made the changes.
#define SHOW_BOOTSCREEN
#define SERIAL_PORT -1
#define BAUDRATE 115200
#define EXTRUDERS 1
#define DEFAULT_NOMINAL_FILAMENT_DIA 1.75
#define TEMP_SENSOR_0 5 //1
#define TEMP_SENSOR_1 0
#define TEMP_SENSOR_2 0
#define TEMP_SENSOR_3 0
#define TEMP_SENSOR_4 0
#define TEMP_SENSOR_5 0
#define TEMP_SENSOR_BED 1
#define TEMP_SENSOR_BOARD 2000
#define TEMP_SENSOR_CHAMBER 0
#define HEATER_CHAMBER_PIN -1 // On/off pin for enclosure heating system
#define DUMMY_THERMISTOR_998_VALUE 25
#define DUMMY_THERMISTOR_999_VALUE 100
#define MAX_REDUNDANT_TEMP_SENSOR_DIFF 10
#define TEMP_RESIDENCY_TIME 1 // (seconds) Time to wait for hotend to "settle" in M109
#define TEMP_WINDOW 2.5F // (°C) Temperature proximity for the "temperature reached" timer
#define TEMP_HYSTERESIS 3 // (°C) Temperature proximity considered "close enough" to the target
#define TEMP_BED_RESIDENCY_TIME 5 // (seconds) Time to wait for bed to "settle" in M190
#define TEMP_BED_WINDOW 1 // (°C) Temperature proximity for the "temperature reached" timer
#define TEMP_BED_HYSTERESIS 3 // (°C) Temperature proximity considered "close enough" to the target
#define TEMP_CHAMBER_HYSTERESIS 3 // (°C) Temperature proximity considered "close enough" to the target
#define HEATER_0_MINTEMP 10
#define HEATER_1_MINTEMP 5
#define HEATER_2_MINTEMP 5
#define HEATER_3_MINTEMP 5
#define HEATER_4_MINTEMP 5
#define HEATER_5_MINTEMP 5
#define BED_MINTEMP 10
#define BOARD_MINTEMP 5
#define CHAMBER_MINTEMP 5
#define HEATER_0_MAXTEMP 300 + 15
#define HEATER_1_MAXTEMP 275
#define HEATER_2_MAXTEMP 275
#define HEATER_3_MAXTEMP 275
#define HEATER_4_MAXTEMP 275
#define HEATER_5_MAXTEMP 275
#define BED_MAXTEMP 120
#define BED_MAXTEMP_SAFETY_MARGIN 10
#define BOARD_MAXTEMP 120
#define CHAMBER_MAXTEMP 100
#define PIDTEMP
#define BANG_MAX 255 // Limits current to nozzle while in bang-bang mode; 255=full current
#define PID_MAX BANG_MAX // Limits current to nozzle while PID is active (see PID_FUNCTIONAL_RANGE below); 255=full current
#define PID_K1 0.97 // Derivative smoothing factor within any PID loop
    #define PID_FUNCTIONAL_RANGE 500 // If the temperature difference between the target temperature and the actual temperature
    #define DEFAULT_Kp 7.00
    #define DEFAULT_Ki 0.50
    #define DEFAULT_Kd 45.00
    #define STEADY_STATE_HOTEND_LINEAR_COOLING_TERM 0.322
    #define STEADY_STATE_HOTEND_QUADRATIC_COOLING_TERM 0.0002
    #define STEADY_STATE_HOTEND_FAN_COOLING_TERM 3.9
#define PIDTEMPBED
#define MAX_BED_POWER 255 // limits duty cycle to bed; 255=full current
    #define DEFAULT_bedKp 120.00
    #define DEFAULT_bedKi 1.50
    #define DEFAULT_bedKd 600.00
#define PREVENT_COLD_EXTRUSION
#define EXTRUDE_MINTEMP 170
#define PREVENT_LENGTHY_EXTRUDE
#define EXTRUDE_MAXLENGTH 1000
#define THERMAL_PROTECTION_HOTENDS // Enable thermal protection for all extruders
#define THERMAL_PROTECTION_BED // Enable thermal protection for the heated bed
#define THERMAL_PROTECTION_CHAMBER // Enable thermal protection for the heated chamber
#define MOVE_BACK_BEFORE_HOMING
    #define MOVE_BACK_BEFORE_HOMING_DISTANCE 1.92f
#define USE_XMIN_PLUG
#define USE_YMIN_PLUG
#define USE_ZMIN_PLUG
#define USE_XMAX_PLUG
#define USE_YMAX_PLUG
#define USE_ZMAX_PLUG
#define ENDSTOPPULLUPS
#define X_MIN_ENDSTOP_INVERTING false // set to true to invert the logic of the endstop.
#define Y_MIN_ENDSTOP_INVERTING false // set to true to invert the logic of the endstop.
#define Z_MIN_ENDSTOP_INVERTING false // set to true to invert the logic of the endstop.
#define X_MAX_ENDSTOP_INVERTING false // set to true to invert the logic of the endstop.
#define Y_MAX_ENDSTOP_INVERTING false // set to true to invert the logic of the endstop.
#define Z_MAX_ENDSTOP_INVERTING false // set to true to invert the logic of the endstop.
#define Z_MIN_PROBE_ENDSTOP_INVERTING false // set to true to invert the logic of the probe.
#define X_DRIVER_TYPE TMC2209
#define Y_DRIVER_TYPE TMC2209
#define Z_DRIVER_TYPE TMC2209
#define E0_DRIVER_TYPE TMC2209
#define DEFAULT_AXIS_STEPS_PER_UNIT \
    { 100, 100, 400, 325 } //E0 280 295
#define DEFAULT_MAX_FEEDRATE \
    { 180, 180, 12, 80 }
#define DEFAULT_MAX_ACCELERATION \
    { 1250, 1250, 400, 4000 }
#define DEFAULT_ACCELERATION 1250 // X, Y, Z and E acceleration for printing moves
#define DEFAULT_RETRACT_ACCELERATION 1250 // E acceleration for retracts
#define DEFAULT_TRAVEL_ACCELERATION 1250 // X, Y, Z acceleration for travel (non printing) moves
#define CLASSIC_JERK
    #define DEFAULT_XJERK 8.0
    #define DEFAULT_YJERK 8.0
    #define DEFAULT_ZJERK 2.0
#define DEFAULT_EJERK 10 // May be used by Linear Advance
#define Z_MIN_PROBE_USES_Z_MIN_ENDSTOP_PIN
#define FIX_MOUNTED_PROBE
#define NOZZLE_TO_PROBE_OFFSET \
    { -29, -3, 0 }
#define MIN_PROBE_EDGE 5
#define XY_PROBE_SPEED 5000
#define Z_PROBE_SPEED_FAST HOMING_FEEDRATE_Z
#define Z_PROBE_SPEED_SLOW (Z_PROBE_SPEED_FAST / 3)
#define MULTIPLE_PROBING 2
#define Z_CLEARANCE_DEPLOY_PROBE 0 // Z Clearance for Deploy/Stow
#define Z_CLEARANCE_BETWEEN_PROBES 1 // Z Clearance between probe points
#define Z_CLEARANCE_MULTI_PROBE 0.5 // Z Clearance between multiple probes
#define Z_AFTER_PROBING 2 // Z position after probing is done
#define Z_PROBE_LOW_POINT -2 // Farthest distance below the trigger-point to go before stopping
#define Z_PROBE_OFFSET_RANGE_MIN -20
#define Z_PROBE_OFFSET_RANGE_MAX 20
#define X_ENABLE_ON 0
#define Y_ENABLE_ON 0
#define Z_ENABLE_ON 0
#define E_ENABLE_ON 0 // For all extruders
#define DISABLE_X false
#define DISABLE_Y false
#define DISABLE_Z false
#define DISABLE_E false // For all extruders
#define DISABLE_INACTIVE_EXTRUDER // Keep only the active extruder enabled
#define DEFAULT_INVERT_X_DIR false
#define DEFAULT_INVERT_Y_DIR false
#define DEFAULT_INVERT_Z_DIR true
#define DEFAULT_INVERT_E0_DIR true
    #define INVERT_X_DIR  has_inverted_x()
    #define INVERT_Y_DIR  has_inverted_y()
    #define INVERT_Z_DIR  has_inverted_z()
    #define INVERT_E0_DIR has_inverted_e()
#define INVERT_E1_DIR false
#define INVERT_E2_DIR false
#define INVERT_E3_DIR false
#define INVERT_E4_DIR false
#define INVERT_E5_DIR false
#define Z_HOMING_HEIGHT 4 // (mm) Minimal Z height before homing (G28) for Z clearance above the bed, clamps, ...
#define X_HOME_DIR 1
#define Y_HOME_DIR -1
#define Z_HOME_DIR -1
#define X_BED_SIZE 180
#define Y_BED_SIZE 180
#define X_MIN_POS -2
#define Y_MIN_POS -3
#define Z_MIN_POS 0
#define X_MAX_POS X_BED_SIZE
#define Y_MAX_POS Y_BED_SIZE
    #define DEFAULT_Z_MAX_POS 185
    #define Z_MIN_LEN_LIMIT 1
    #define Z_MAX_LEN_LIMIT 10000
    #define Z_MAX_POS (get_z_max_pos_mm())
#define MIN_SOFTWARE_ENDSTOPS
    #define MIN_SOFTWARE_ENDSTOP_X
    #define MIN_SOFTWARE_ENDSTOP_Y
    #define MIN_SOFTWARE_ENDSTOP_Z
#define MAX_SOFTWARE_ENDSTOPS
    #define MAX_SOFTWARE_ENDSTOP_X
    #define MAX_SOFTWARE_ENDSTOP_Y
    #define MAX_SOFTWARE_ENDSTOP_Z
#define AUTO_BED_LEVELING_BILINEAR
#define RESTORE_LEVELING_AFTER_G28 false
    #define ENABLE_LEVELING_FADE_HEIGHT
    #define SEGMENT_LEVELED_MOVES
    #define LEVELED_SEGMENT_LENGTH 5.0 // (mm) Length of all segments (except the last one)
    #define GRID_MAX_POINTS_X 4
    #define GRID_MAX_POINTS_Y GRID_MAX_POINTS_X
        #define EXTRAPOLATE_BEYOND_GRID
#define MANUAL_X_HOME_POS 180.4
#define Z_SAFE_HOMING
    #define Z_SAFE_HOMING_X_POINT (147.4) // X point for Z homing when homing all axes (G28).
    #define Z_SAFE_HOMING_Y_POINT (21.1) // Y point for Z homing when homing all axes (G28).
#define HOMING_FEEDRATE_XY (3000)
#define HOMING_FEEDRATE_Z (6 * 60)
#define SKEW_CORRECTION
    #define XY_DIAG_AC 282.8427124746
    #define XY_DIAG_BD 282.8427124746
    #define XY_SIDE_AD 200
    #define XY_SKEW_FACTOR 0.0
    #define SKEW_CORRECTION_FOR_Z
        #define XZ_DIAG_AC 282.8427124746
        #define XZ_DIAG_BD 282.8427124746
        #define YZ_DIAG_AC 282.8427124746
        #define YZ_DIAG_BD 282.8427124746
        #define YZ_SIDE_AD 200
        #define XZ_SKEW_FACTOR 0.0
        #define YZ_SKEW_FACTOR 0.0
#define SKEW_CORRECTION_GCODE
#define HOST_KEEPALIVE_FEATURE // Disable this if your host doesn't like keepalive messages
#define DEFAULT_KEEPALIVE_INTERVAL 2 // Number of seconds between "busy" messages. Set with M113.
#define BUSY_WHILE_HEATING // Some hosts require "busy" messages even during heating
#define PREHEAT_1_LABEL "PLA"
#define PREHEAT_1_TEMP_HOTEND 215
#define PREHEAT_1_TEMP_BED 60
#define PREHEAT_1_FAN_SPEED 0 // Value from 0 to 255
#define PREHEAT_2_LABEL "PET"
#define PREHEAT_2_TEMP_HOTEND 230
#define PREHEAT_2_TEMP_BED 85
#define PREHEAT_2_FAN_SPEED 0 // Value from 0 to 255
#define NOZZLE_PARK_FEATURE
    #define NOZZLE_PARK_POINT \
        { (X_MAX_POS - 10), (Y_MAX_POS - 10), 20 }
        #define NOZZLE_PARK_POINT_M600 \
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

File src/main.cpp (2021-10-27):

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

/* Includes ------------------------------------------------------------------*/
#include "main.h"
#include "cmsis_os.h"
#include "fatfs.h"
#ifdef BUDDY_ENABLE_WUI
    #include "wui.h"
#endif
#include "usb_device.h"
#include "usb_host.h"
#include "buffered_serial.hpp"

/* USER CODE BEGIN Includes */
#include "sys.h"
#include "app.h"
#include "dbg.h"
#include "wdt.h"
#include "diag.h"
#include "dump.h"
#include "timer_defaults.h"
#include "thread_measurement.h"
#include "metric_handlers.h"
#include "Z_probe.h"
#include "hwio_pindef.h"
#include "gui.hpp"
#include "config_a3ides2209_02.h"
#include "eeprom.h"
#include "crc32.h"
#include "w25x.h"
#include "llama.h"

/* USER CODE END Includes */

ADC_HandleTypeDef hadc1;

I2C_HandleTypeDef hi2c1;

RTC_HandleTypeDef hrtc;
SPI_HandleTypeDef hspi2;
SPI_HandleTypeDef hspi3;
DMA_HandleTypeDef hdma_spi2_tx;
DMA_HandleTypeDef hdma_spi2_rx;

TIM_HandleTypeDef htim1;
TIM_HandleTypeDef htim2;
TIM_HandleTypeDef htim3;
TIM_HandleTypeDef htim14;

static UART_HandleTypeDef huart1;
UART_HandleTypeDef huart2;
UART_HandleTypeDef huart6;
DMA_HandleTypeDef hdma_usart1_rx;
DMA_HandleTypeDef hdma_usart2_rx;
DMA_HandleTypeDef hdma_usart6_rx;

osThreadId defaultTaskHandle;
osThreadId displayTaskHandle;
osThreadId webServerTaskHandle;
/* USER CODE BEGIN PV */
int HAL_IWDG_Reset = 0;
int HAL_GPIO_Initialized = 0;
int HAL_ADC_Initialized = 0;
int HAL_PWM_Initialized = 0;
int HAL_SPI_Initialized = 0;
/* USER CODE END PV */

void SystemClock_Config(void);
static void MX_GPIO_Init(void);
static void MX_DMA_Init(void);
static void MX_I2C1_Init(void);
static void MX_ADC1_Init(void);
static void MX_USART1_UART_Init(void);
static void MX_TIM1_Init(void);
static void MX_TIM3_Init(void);
static void MX_SPI2_Init(void);
static void MX_USART2_UART_Init(void);
static void MX_USART6_UART_Init(void);
static void MX_SPI3_Init(void);
static void MX_TIM2_Init(void);
static void MX_TIM14_Init(void);
static void MX_RTC_Init(void);
void StartDefaultTask(void const *argument);
void StartDisplayTask(void const *argument);
void iwdg_warning_cb(void);

/* USER CODE BEGIN 0 */
#include "uartslave.h"
#include "putslave.h"

uartrxbuff_t uart1rxbuff;
static uint8_t uart1rx_data[200];

uartrxbuff_t uart6rxbuff;
uint8_t uart6rx_data[128];
uartslave_t uart6slave;
char uart6slave_line[32];

static volatile uint32_t minda_falling_edges = 0;
uint32_t get_Z_probe_endstop_hits() { return minda_falling_edges; }

/*
    #define RCC_FLAG_LSIRDY                  ((uint8_t)0x61)
    #define RCC_FLAG_BORRST                  ((uint8_t)0x79)
    #define RCC_FLAG_PINRST                  ((uint8_t)0x7A)
    #define RCC_FLAG_PORRST                  ((uint8_t)0x7B)
    #define RCC_FLAG_SFTRST                  ((uint8_t)0x7C)
    #define RCC_FLAG_IWDGRST                 ((uint8_t)0x7D)
    #define RCC_FLAG_WWDGRST                 ((uint8_t)0x7E)
    #define RCC_FLAG_LPWRRST                 ((uint8_t)0x7F)
    */

/**
 * @brief initialization of eeprom and prerequisites, to be able to use
 *        it to initialize static variables and objects
 * This is called during startup before main and before initialization
 *        of static variables but after setting them to 0
 */
extern "C" void EepromSystemInit() {
    //__HAL_RCC_GET_FLAG(RCC_FLAG_LPWRRST);
    //__HAL_RCC_GET_FLAG(RCC_FLAG_WWDGRST);
    if (__HAL_RCC_GET_FLAG(RCC_FLAG_IWDGRST))
        HAL_IWDG_Reset = 1;
    //__HAL_RCC_GET_FLAG(RCC_FLAG_SFTRST);
    //__HAL_RCC_GET_FLAG(RCC_FLAG_PORRST);
    //__HAL_RCC_GET_FLAG(RCC_FLAG_PINRST);
    //__HAL_RCC_GET_FLAG(RCC_FLAG_BORRST);
    __HAL_RCC_CLEAR_RESET_FLAGS();

    /* Reset of all peripherals, Initializes the Flash interface and the Systick. */
    HAL_Init(); //it is low level enought to be run in startup script
    /* Configure the system clock */
    SystemClock_Config();

    diag_check_fastboot();

    MX_I2C1_Init();
    crc32_init();

    int irq = __get_PRIMASK() & 1;
    __enable_irq();

    // initialize Llama Eeprom first so that old settings don't get overwritten
    // by Prusa's extension of their EEPROM address range from 0x500-0x600 to 0x500-0x700
    eeprom_llama_init();
    eeprom_init();

    if (irq == 0)
        __disable_irq();
}

/**
  * @brief  The application entry point.
  *   There is EepromSystemInit function called before main
  *   which is alowing early access to eeprom
  * @retval int
  */
int main(void) {
    /* Initialize all configured peripherals */
    MX_GPIO_Init();
    MX_DMA_Init();
    MX_ADC1_Init();
    MX_USART1_UART_Init();
    MX_TIM1_Init();
    MX_TIM3_Init();
    MX_SPI2_Init();
    MX_USART2_UART_Init();
    MX_USART6_UART_Init();
    MX_SPI3_Init();
    MX_TIM2_Init();
    MX_TIM14_Init();
    MX_RTC_Init();

    HAL_GPIO_Initialized = 1;
    HAL_ADC_Initialized = 1;
    HAL_PWM_Initialized = 1;
    HAL_SPI_Initialized = 1;

    w25x_init(); //SPI flash
    eeprom_init_status_t status = eeprom_init();
    if (status == EEPROM_INIT_Defaults || status == EEPROM_INIT_Upgraded) {
        // this means we are either starting from defaults or after a FW upgrade -> invalidate the XFLASH dump, since it is not relevant anymore
        dump_in_xflash_reset();
    }

    wdt_iwdg_warning_cb = iwdg_warning_cb;

    buddy::hw::BufferedSerial::uart2.Open();

    uartrxbuff_init(&uart1rxbuff, &huart1, &hdma_usart1_rx, sizeof(uart1rx_data), uart1rx_data);
    HAL_UART_Receive_DMA(&huart1, uart1rxbuff.buffer, uart1rxbuff.buffer_size);
    uartrxbuff_reset(&uart1rxbuff);

    uartrxbuff_init(&uart6rxbuff, &huart6, &hdma_usart6_rx, sizeof(uart6rx_data), uart6rx_data);
    HAL_UART_Receive_DMA(&huart6, uart6rxbuff.buffer, uart6rxbuff.buffer_size);
    uartrxbuff_reset(&uart6rxbuff);
    uartslave_init(&uart6slave, &uart6rxbuff, &huart6, sizeof(uart6slave_line), uart6slave_line);
    putslave_init(&uart6slave);

    /* USER CODE END 2 */

    static metric_handler_t *handlers[] = {
        &metric_handler_syslog,
        NULL
    };
    metric_system_init(handlers);
    /* USER CODE BEGIN RTOS_MUTEX */
    /* add mutexes, ... */
    /* USER CODE END RTOS_MUTEX */

    /* USER CODE BEGIN RTOS_SEMAPHORES */
    /* add semaphores, ... */
    /* USER CODE END RTOS_SEMAPHORES */

    /* USER CODE BEGIN RTOS_TIMERS */
    /* start timers, add new ones, ... */
    /* USER CODE END RTOS_TIMERS */

    /* Create the thread(s) */
    /* definition and creation of defaultTask */
    osThreadDef(defaultTask, StartDefaultTask, osPriorityNormal, 0, 1024);
    defaultTaskHandle = osThreadCreate(osThread(defaultTask), NULL);

    /* definition and creation of displayTask */
    osThreadDef(displayTask, StartDisplayTask, osPriorityNormal, 0, 2048);
    displayTaskHandle = osThreadCreate(osThread(displayTask), NULL);

#ifdef BUDDY_ENABLE_WUI
    /* definition and creation of webServerTask */
    osThreadDef(webServerTask, StartWebServerTask, osPriorityNormal, 0, BUDDY_WEB_STACK_SIZE);
    webServerTaskHandle = osThreadCreate(osThread(webServerTask), NULL);
#endif

    /* USER CODE BEGIN RTOS_THREADS */
    /* add threads, ... */
    /* definition and creation of measurementTask */
    osThreadDef(measurementTask, StartMeasurementTask, osPriorityNormal, 0, 512);
    osThreadCreate(osThread(measurementTask), NULL);

    /* USER CODE END RTOS_THREADS */

    /* USER CODE BEGIN RTOS_QUEUES */
    /* add queues, ... */
    /* USER CODE END RTOS_QUEUES */

    /* Start scheduler */
    osKernelStart();

    /* We should never get here as control is now taken by the scheduler */

    /* Infinite loop */
    /* USER CODE BEGIN WHILE */
    while (1) {
        /* USER CODE END WHILE */

        /* USER CODE BEGIN 3 */
    }
    /* USER CODE END 3 */
}

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
/* USER CODE BEGIN 4 */
extern void st7789v_spi_tx_complete(void);
void HAL_SPI_TxCpltCallback(SPI_HandleTypeDef *hspi) {
    st7789v_spi_tx_complete();
}

void HAL_UART_TxCpltCallback(UART_HandleTypeDef *haurt) {
    if (haurt == &huart2)
        buddy::hw::BufferedSerial::uart2.WriteFinishedISR();
}

void HAL_UART_RxHalfCpltCallback(UART_HandleTypeDef *huart) {
    if (huart == &huart2)
        buddy::hw::BufferedSerial::uart2.FirstHalfReachedISR();
    else if (huart == &huart6)
        uartrxbuff_rxhalf_cb(&uart6rxbuff);
}

void HAL_UART_RxCpltCallback(UART_HandleTypeDef *huart) {
    if (huart == &huart1)
        uartrxbuff_rxcplt_cb(&uart1rxbuff);
    else if (huart == &huart2)
        buddy::hw::BufferedSerial::uart2.SecondHalfReachedISR();
    else if (huart == &huart6)
        uartrxbuff_rxcplt_cb(&uart6rxbuff);
}

void HAL_GPIO_EXTI_Callback(uint16_t GPIO_Pin) {
    switch (GPIO_Pin) {
    case Z_MIN_Pin:
        ++minda_falling_edges;
        break;
    }
}

/* USER CODE END 4 */

/* USER CODE BEGIN Header_StartDefaultTask */
/**
  * @brief  Function implementing the defaultTask thread.
  * @param  argument: Not used
  * @retval None
  */
/* USER CODE END Header_StartDefaultTask */
void StartDefaultTask(void const *argument) {
    /* init code for USB_DEVICE */
    MX_USB_DEVICE_Init();

    /* init code for USB_HOST */
    MX_USB_HOST_Init();

    /* init code for FATFS */
    MX_FATFS_Init();

    /* init code for LWIP */
    //MX_LWIP_Init();

    /* USER CODE BEGIN 5 */
    app_run();
    /* Infinite loop */
    for (;;) {
        osDelay(1);
    }
    /* USER CODE END 5 */
}

/* USER CODE BEGIN Header_StartDisplayTask */
/**
* @brief Function implementing the displayTask thread.
* @param argument: Not used
* @retval None
*/
/* USER CODE END Header_StartDisplayTask */
void StartDisplayTask(void const *argument) {
    /* USER CODE BEGIN StartDisplayTask */
    gui_run();
    /* Infinite loop */
    for (;;) {
        osDelay(1);
    }
    /* USER CODE END StartDisplayTask */
}

/**
  * @brief  Period elapsed callback in non blocking mode
  * @note   This function is called  when TIM6 interrupt took place, inside
  * HAL_TIM_IRQHandler(). It makes a direct call to HAL_IncTick() to increment
  * a global variable "uwTick" used as application time base.
  * @param  htim : TIM handle
  * @retval None
  */
void HAL_TIM_PeriodElapsedCallback(TIM_HandleTypeDef *htim) {
    /* USER CODE BEGIN Callback 0 */
    if (htim->Instance == TIM6) {
        wdt_tick_1ms();
        HAL_IncTick();
    } else if (htim->Instance == TIM14) {
        app_tim14_tick();
    }
    /* USER CODE END Callback 1 */
}

/**
  * @brief  This function is executed in case of error occurrence.
  * @retval None
  */
void Error_Handler(void) {
    /* USER CODE BEGIN Error_Handler_Debug */
    /* User can add his own implementation to report the HAL error return state */
    app_error();
    /* USER CODE END Error_Handler_Debug */
}

void iwdg_warning_cb(void) {
    DUMP_IWDGW_TO_CCRAM(0x10);
    wdt_iwdg_refresh();
    dump_to_xflash();
    while (1)
        ;
    //	sys_reset();
}

#ifdef USE_FULL_ASSERT
/**
  * @brief  Reports the name of the source file and the source line number
  *         where the assert_param error has occurred.
  * @param  file: pointer to the source file name
  * @param  line: assert_param error line source number
  * @retval None
  */
void assert_failed(uint8_t *file, uint32_t line) {
    /* USER CODE BEGIN 6 */
    /* User can add his own implementation to report the file name and line number,
     tex: printf("Wrong parameters value: file %s on line %d\r\n", file, line) */
    app_assert(file, line);
    /* USER CODE END 6 */
}
#endif /* USE_FULL_ASSERT */

/************************ (C) COPYRIGHT STMicroelectronics *****END OF FILE****/

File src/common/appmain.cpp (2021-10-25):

//appmain.cpp - arduino-like app start

#include "appmain.hpp"
#include "app.h"
#include "app_metrics.h"
#include "dbg.h"
#include "cmsis_os.h"
#include "config.h"
#include "dbg.h"
#include "adc.h"
#include "Jogwheel.hpp"
#include "hwio.h"
#include "sys.h"
#include "gpio.h"
#include "sound.hpp"
#include "language_eeprom.hpp"
#include "usbd_cdc_if.h"

#ifdef SIM_HEATER
    #include "sim_heater.h"
#endif //SIM_HEATER

#ifdef SIM_MOTION
    #include "sim_motion.h"
#endif //SIM_MOTION

#include "uartslave.h"
#include "marlin_server.h"
#include "bsod.h"
#include "eeprom.h"
#include "diag.h"
#include "safe_state.h"
#include "crc32.h"
#include "ff.h"
#include "dump.h"
#include "llama.h"

#include <Arduino.h>
#include "trinamic.h"
#include "../Marlin/src/module/configuration_store.h"

#ifdef NEW_FANCTL
    #include "fanctl.h"
CFanCtl fanctl0 = CFanCtl(
    buddy::hw::fan0pwm,
    buddy::hw::fan0tach,
    FANCTL0_PWM_MIN, FANCTL0_PWM_MAX,
    FANCTL0_RPM_MIN, FANCTL0_RPM_MAX,
    FANCTL0_PWM_THR,
    is_autofan_t::no);
CFanCtl fanctl1 = CFanCtl(
    buddy::hw::fan1pwm,
    buddy::hw::fan1tach,
    FANCTL1_PWM_MIN, FANCTL1_PWM_MAX,
    FANCTL1_RPM_MIN, FANCTL1_RPM_MAX,
    FANCTL1_PWM_THR,
    is_autofan_t::yes);
#endif //NEW_FANCTL

#define DBG _dbg0 //debug level 0
//#define DBG(...)  //disable debug

extern void USBSerial_put_rx_data(uint8_t *buffer, uint32_t length);
extern void app_cdc_rx(uint8_t *buffer, uint32_t length);

extern void reset_trinamic_drivers();

extern "C" {

extern uartrxbuff_t uart6rxbuff; // PUT rx buffer
extern uartslave_t uart6slave;   // PUT slave

#ifdef BUDDY_ENABLE_ETHERNET
extern osThreadId webServerTaskHandle; // Webserver thread(used for fast boot mode)
#endif                                 //BUDDY_ENABLE_ETHERNET

void app_setup(void) {
    if (INIT_TRINAMIC_FROM_MARLIN_ONLY == 0) {
        init_tmc();
    } else {
        init_tmc_bare_minimum();
    }

    // enable cdc
    usbd_cdc_register_receive_fn(app_cdc_rx);

    setup();

    marlin_server_settings_load(); // load marlin variables from eeprom
    //DBG("after init_tmc (%ld ms)", HAL_GetTick());
}

void app_idle(void) {
    Buddy::Metrics::RecordMarlinVariables();
    Buddy::Metrics::RecordRuntimeStats();
    Buddy::Metrics::RecordPrintFilename();
    osDelay(0); // switch to other threads - without this is UI slow during printing
}

void app_run(void) {
    DBG("app_run");

#ifdef BUDDY_ENABLE_ETHERNET
    if (diag_fastboot)
        osThreadResume(webServerTaskHandle);
#endif //BUDDY_ENABLE_ETHERNET

    LangEEPROM::getInstance();

    marlin_server_init();
    marlin_server_idle_cb = app_idle;

    adc_init();

#ifdef SIM_HEATER
    sim_heater_init();
#endif //SIM_HEATER

    //DBG("before setup (%ld ms)", HAL_GetTick());
    if (diag_fastboot || (!sys_fw_is_valid())) {
        if (!sys_fw_is_valid()) // following code will be done only with invalidated firmware
        {
            hwio_safe_state(); // safe states
            for (int i = 0; i < hwio_fan_get_cnt(); ++i)
                hwio_fan_set_pwm(i, 0); // disable fans
        }
        if (INIT_TRINAMIC_FROM_MARLIN_ONLY == 0) {
            init_tmc();
        }
        reset_trinamic_drivers();
    } else {
        app_setup();
        marlin_server_start_processing();
    }
    //DBG("after setup (%ld ms)", HAL_GetTick());

    if (eeprom_init() == EEPROM_INIT_Defaults && marlin_server_processing()) {
        settings.reset();
    }

    while (1) {
        if (marlin_server_processing()) {
            loop();
        }
        uartslave_cycle(&uart6slave);
        marlin_server_loop();
        osDelay(0); // switch to other threads - without this is UI slow
#ifdef JOGWHEEL_TRACE
        static int signals = jogwheel_signals;
        if (signals != jogwheel_signals) {
            signals = jogwheel_signals;
            DBG("%d %d", signals, jogwheel_encoder);
        }
#endif //JOGWHEEL_TRACE
#ifdef SIM_MOTION_TRACE_X
        static int32_t x = sim_motion_pos[0];
        if (x != sim_motion_pos[0]) {
            x = sim_motion_pos[0];
            DBG("X:%li", x);
        }
#endif //SIM_MOTION_TRACE_X
#ifdef SIM_MOTION_TRACE_Y
        static int32_t y = sim_motion_pos[1];
        if (y != sim_motion_pos[1]) {
            y = sim_motion_pos[1];
            DBG("Y:%li", y);
        }
#endif //SIM_MOTION_TRACE_Y
#ifdef SIM_MOTION_TRACE_Z
        static int32_t z = sim_motion_pos[2];
        if (z != sim_motion_pos[2]) {
            z = sim_motion_pos[2];
            DBG("Z:%li", z);
        }
#endif //SIM_MOTION_TRACE_Z
#if defined(FANCTL0_TRACE) && defined(FANCTL0_TRACE)
        static uint16_t rpm0_tmp = 0;
        static uint16_t rpm1_tmp = 0;
        uint16_t rpm0 = fanctl0.getActualRPM();
        uint16_t rpm1 = fanctl1.getActualRPM();
        if ((rpm0_tmp != rpm0) || (rpm1_tmp != rpm1)) {
            rpm0_tmp = rpm0;
            rpm1_tmp = rpm1;
            _dbg("rpm0: %-5u rpm1: %-5u", rpm0, rpm1);
        }
#else //defined(FANCTL0_TRACE) && defined(FANCTL0_TRACE)
    #ifdef FANCTL0_TRACE
        static uint16_t rpm0_tmp = 0;
        uint16_t rpm0 = fanctl0.getActualRPM();
        if (rpm0_tmp != rpm0) {
            rpm0_tmp = rpm0;
            _dbg("rpm0: %u", rpm0);
        }
    #endif //FANCTL0_TRACE
    #ifdef FANCTL1_TRACE
        static uint16_t rpm1_tmp = 0;
        uint16_t rpm1 = fanctl1.getActualRPM();
        if (rpm1_tmp != rpm1) {
            rpm1_tmp = rpm1;
            _dbg("rpm1: %u", rpm1);
        }
    #endif //FANCTL1_TRACE
#endif     //defined(FANCTL0_TRACE) && defined(FANCTL0_TRACE)
    }
}

void app_error(void) {
    bsod("app_error");
}

void app_assert(uint8_t *file, uint32_t line) {
    bsod("app_assert");
}

void app_cdc_rx(uint8_t *buffer, uint32_t length) {
    if (!marlin_server_get_exclusive_mode()) // serial line is disabled in exclusive mode
        USBSerial_put_rx_data(buffer, length);
}

void adc_tick_1ms(void) {
    adc_cycle();
#ifdef SIM_HEATER
    static uint8_t cnt_sim_heater = 0;
    if (++cnt_sim_heater >= 50) // sim_heater freq = 20Hz
    {
        sim_heater_cycle();
        cnt_sim_heater = 0;
    }
#endif //SIM_HEATER

#ifdef SIM_MOTION
    sim_motion_cycle();
#endif //SIM_MOTION
}

void app_tim14_tick(void) {
#ifdef NEW_FANCTL
    fanctl_tick();
#endif //NEW_FANCTL
#ifndef HAS_GUI
    #error "HAS_GUI not defined."
#elif HAS_GUI
    jogwheel.Update1msFromISR();
#endif
    Sound_Update1ms();
    //hwio_update_1ms();
    adc_tick_1ms();
}

} // extern "C"

//cpp code

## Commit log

2021-10-25 Add Llama settings menu, with extruder, fan speed, and skew correction
    [Configuration_A3ides_2209_MINI.h]
2021-10-25 Automatically save PID settings to EEPROM after M301, M304, and M303 U1
2021-10-25 Add new skew correction STL and spreadsheet
    [skew.stl]
2021-10-25 Add note to use M303 E-2 to autotune the bed PID
2021-10-25 Use alternative method to reverse extruder direction, since Marlin does not like negative e-steps
    [MItem_tools.cpp, marlin_server.cpp]
2021-10-27 Build and other fixes for 4.3.3 upgrade
    [MItem_tools.cpp, main.cpp, marlin_server.cpp]
2021-11-13 Raise max temps
    [Configuration_A3ides_2209_MINI.h]

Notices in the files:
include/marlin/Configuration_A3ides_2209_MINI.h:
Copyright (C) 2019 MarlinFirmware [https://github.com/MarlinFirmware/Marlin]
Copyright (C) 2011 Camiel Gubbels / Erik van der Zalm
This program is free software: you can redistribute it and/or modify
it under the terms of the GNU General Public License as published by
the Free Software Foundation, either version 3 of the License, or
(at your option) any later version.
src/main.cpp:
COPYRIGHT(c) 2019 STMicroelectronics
